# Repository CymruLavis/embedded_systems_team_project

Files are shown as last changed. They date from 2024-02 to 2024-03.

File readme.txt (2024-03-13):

Note to developers: after connecting this repo to your local machine any additional 
class files that need to be used in execution need to be added to the CMakeLists.txt file. That is done by adding 
src/<filename>.cpp to the add_exacutable chain

to run the program make sure you are in the build directory then run the following

>> make
>> ./cocktail_machine

make is the command that will compile the project with our cmake architecture
./cocktail_machine executes/runs the project

SMART DRINKER COCKTAIL MACHINE PROJECT  
![Logo]()

This is our team project for embedded systems at the University of Glasgow with team members:
Ethan Lavis
Daraigh O'Toole Eglington
Joshua Varghese
Roykeane Syangu

The goal of this project is to create an automcatic cocktail dispensor using real time embedded programming on the raspberry pi

![CAD]()

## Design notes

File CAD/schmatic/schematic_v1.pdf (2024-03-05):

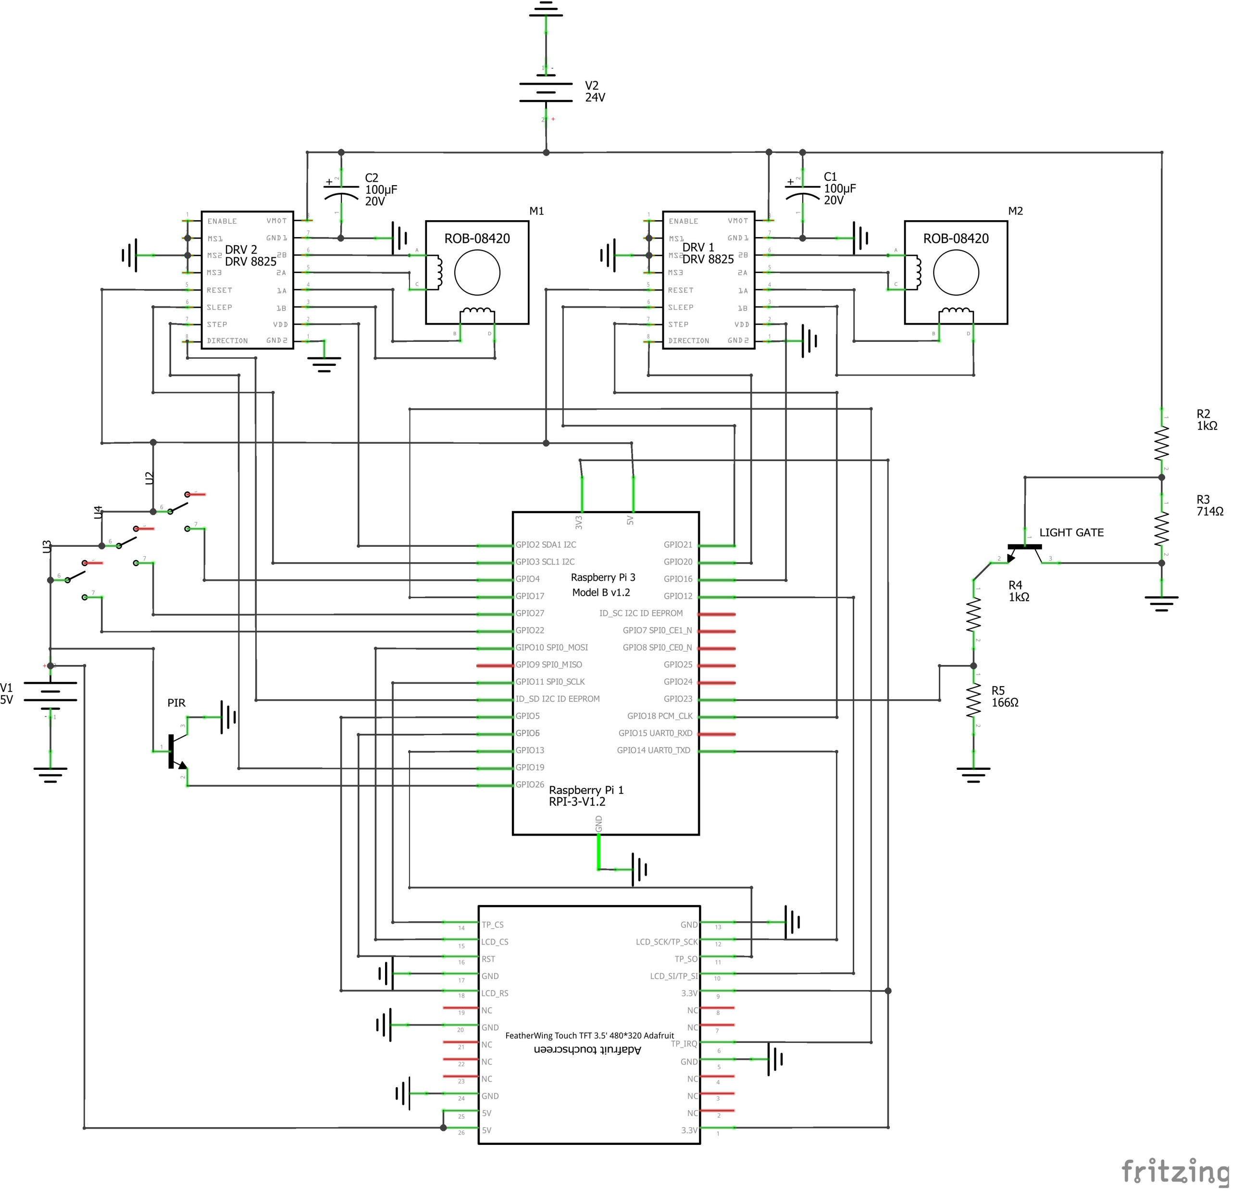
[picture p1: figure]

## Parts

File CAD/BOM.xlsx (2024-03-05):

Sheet: DETAIL_BOM
DESCRIPTION | MANUFACTURER PART NUMBER AND DATA SHEET | QUANTITY | UNIT COST | COST | LINK AND SUPPLIER
VERTICAL ACTUATOR STEPPER DRIVE SET | CABLE PIN OUT TO CONTROLLER IN DATASHEET (https://www.omc-stepperonline.com/3-pcs-e-series-nema-17-bipolar-42ncm-59-49oz-in-1-5a-42x42x38mm-4-wires-w-1m-cable-connector-3-17he15-1504s) | 1 | 14.33 | 14.33 | OMC-STEPPER LINK TO PART CLICK HERE (https://www.omc-stepperonline.com/3-pcs-e-series-nema-17-bipolar-42ncm-59-49oz-in-1-5a-42x42x38mm-4-wires-w-1m-cable-connector-3-17he15-1504s) | https://www.omc-stepperonline.com/e-series-nema-17-bipolar-42ncm-59-49oz-in-1-5a-42x42x38mm-4-wires-w-1m-cable-connector-17he15-1504s
Optic dispensors |  | 6 | 2.75 | 16.5 | ASCOT WHOLESALE LINK TO PART CLICK HERE (https://www.ascotwholesale.co.uk/25ml-black-solo-measure?gad_source=1) | https://www.ascotwholesale.co.uk/25ml-black-solo-measure?gad_source=1
TUBE 8x1.5mm 700mm long. Use the free custom cutting service. |  | 1 | 5.96 | 5.96 | METALS4U LINK TO PART CLICK HERE (https://www.metals4u.co.uk/materials/mild-steel/mild-steel-tube/tube/9135-p) | https://www.metals4u.co.uk/materials/mild-steel/mild-steel-tube/tube/9135-p
Square Box Section 12.7x12.7x1.2 700mm Long Use the free custom cutting service |  | 4 | 1.64 | 6.56 | METALS4U LINK TO PART CLICK HERE (https://www.metals4u.co.uk/materials/mild-steel/mild-steel-box-section/2371-p) | https://www.metals4u.co.uk/materials/mild-steel/mild-steel-box-section/2371-p
MOTION DETECTOR PIR | PIR sensor - works like a switch!! (https://www.mpja.com/download/31227sc.pdf) | 1 | 3 | 3 | PIHIT LINK TO PART CLICK HERE (https://thepihut.com/products/pir-motion-sensor-module) | https://thepihut.com/products/pir-motion-sensor-module | https://shop.pimoroni.com/products/pir-motion-sensor-1?variant=39364784881747
 |  |  | TOTAL: | 46.35
STEPPER MOTOR DRIVER OPTION 1 STEP/DIR | DRV8825 DRIVER DATASHEET (https://www.ti.com/lit/ds/symlink/drv8825.pdf) | 2 | 4.5 | 9 | https://www.amazon.co.uk/DRV8825-Stepper-Suitable-8-2V-45V-Printer/dp/B0CCRXGKLV?hvadid=676281988980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 |  | https://www.pololu.com/product/2133 | https://www.ti.com/lit/ds/symlink/drv8825.pdf | https://how2electronics.com/control-stepper-motor-with-drv8825-raspberry-pi-pico/
RADIAL BEARINGS |  | 4 | 1.25 | 5 | https://www.amazon.co.uk/sourcingmap-Groove-Bearing-Double-Bearings/dp/B07FDYTJS5
THRUST BEARING |  | 2 | 3 | 6 | https://www.amazon.co.uk/sourcingmap-Single-Direction-Thrust-Bearings/dp/B07G8QDQVM
3.5" Touch Screen (mixed reviews, fast shipping, uses 13/20 rows of our pins) | SCREEN DATASHEET/MANUAL (https://www.osoyoo.com/manual/2022013800.pdf) | 1 | 18.99 | 18.99 | https://www.amazon.co.uk/OSOYOO-Monitor-Raspberry-480x320-Interface/dp/B085TC5YMR?rnid=428432031
VELCRO STRAP |  | 1 | 3.2 | 3.2 | https://www.amazon.co.uk/VELCRO%C2%AE-Brand-ONE-WRAP%C2%AE-double-Strapping/dp/B0777LN5VP
 |  |  | TOTAL: | 42.19
MICRO SWITCH | USE A SPDT switch in circuit diagram set to n.o | 1 | FREE | 0
Omron Through Beam Photoelectric Sensor | EE-SX4009-P1 (https://omronfs.omron.com/en_US/ecb/products/pdf/en-ee_sx3009_p1_4009_p1.pdf) | 1 | DARA | 0 | https://uk.rs-online.com/web/p/photoelectric-sensors/8074251
FASTENERS |  |  | DARA | 0
3D PRINTS |  |  | DARA | 0
INSERTS BRASS M3&M4 |  |  | DARA | 0
Total Cost
 | SPDT

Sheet: FASTENERS
M | PART | LENGTH | DEPTH | HEAD WDITH
M4 | NUT | 6.87 | 3 | 6.9 | PART NUMBER | SIZE | TYPE | LENGTH | QTY. | STOCK?
M3 | NUT | 5.4 | 2.23 | 5.45 | DIN 912 M2 x 20 --- 20N | M2 | SKT | 20 | 4 | CHECK
M3 | CSK | 12 |  | 5.5 | Hexagon Nut ISO 4032 - M2 - D - N | M2 | NUT | 5.5 | 8 | YES
M3 | CSK | 20 |  | 5.3 | Hexagon Nut ISO 4032 - M3 - D - N | M3 | NUT | 5.5 | 100
M3 | POSY | 6 |  | 5.9 | DIN 7991 - M3 x 12 --- 8.8N | M3 | CSK | 12 | 21
M3 | POSY | 12 |  | 6 | DIN 912 M3 x 10 --- 10N | M3 | SKT | 10 | 6 | USE M3X12
M4 | CSK | 10 |  | 7.7 | DIN 7991 - M3 x 16 | M3 | CSK | 16 | 50 | ORDER | https://www.amazon.co.uk/ORANXIN-Hex-Bolts-Screws-Countersunk/dp/B08BHL1BBZ?th=1 | https://www.accu.co.uk/order
M4 | CSK | 25 |  | 8.3 | DIN 912 M3 x 12 --- 12N | M3 | SKT | 12 | 32 | HAVE
M4 | POSY | 12 |  | 7.75 | DIN 912 M2 x 6 --- 6N | M2 | SKT | 6 | 4 | CHECK
 |  |  |  |  | DIN 912 M3 x 30 --- 30N | M3 | SKT | 30 | 24 | ORDER |  | https://www.accu.co.uk/metric-cap-head-screws/2805-SSC-M3-30-A2
 |  |  |  |  | Washer DIN 125 - A 3.2 | M3 | WASHER | 1.2 | 24 | HAVE

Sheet: Sheet3
M | PART | LENGTH | DEPTH | HEAD WDITH
M3 | NUT | 5.4 | 2.23 | 5.45
M3 | CSK | 12 |  | 5.5
M3 | POSY | 6 |  | 5.9
M3 | CSK | 20 |  | 5.3
M3 | POSY | 12 |  | 6
M4 | POSY | 12 |  | 7.75
M4 | CSK | 10 |  | 7.7
M4 | NUT | 6.87 | 3 | 6.9
M4 | CSK | 25 |  | 8.3
 |  |  |  |  | M3 | CSK | 12 | 5.5
 |  |  |  |  | M3 | CSK | 20 | 5.3
 |  |  |  |  | M3 | POSY | 6 | 5.9
 |  |  |  |  | M3 | POSY | 12 | 6
 |  |  |  |  | M4 | CSK | 10 | 7.7
 |  |  |  |  | M4 | CSK | 25 | 8.3
 |  |  |  |  | M4 | POSY | 12 | 7.75

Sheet: FASTENER BOM
PART NUMBER | SIZE | TYPE | LENGTH | QTY.
DIN 7991 - M3 x 8 --- 8N | M3 | CSK | 8 | 8
DIN 912 M3 x 10 --- 10N | M3 | SKT | 10 | 8
DIN 912 M3 x 12 --- 12N | M3 | SKT | 12 | 4
DIN 7991 - M3 x 12 --- 8.8N | M3 | CSK | 12 | 8
DIN 7991 - M3 x 16 --- 12.8N | M3 | CSK | 16 | 6
DIN 7991 - M3 x 16 --- 16N | M3 | CSK | 16 | 8
DIN 912 M3 x 16 --- 16N | M3 | SKT | 16 | 4
DIN 7991 - M4 x 16 --- 16N | M3 | CSK | 16 | 18
DIN 912 M3 x 25 --- 18N | M3 | SKT | 25 | 24
DIN 7991 - M3 x 30 --- 12N | M3 | CSK | 30 | 4

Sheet: SPIN VS PUMPED
 | Weighting: | SPINNING | SUM: | PUMPED | SUM: | BOM PUMPED SOLTUON | QUANTITY | UNIT COST | TOTAL COST | LINK
SPEED | 1 | 2 | 2 | 2 | 2 | 12V MOTORS | 6 | 4 | 24
COST | 1 | 3 | 3 | 1 | 1 | BEARINGS | 18 | 0.25 | 4.5
MECHANICAL COMPLEXITY | 1 | 1 | 1 | 3 | 3 | PLASTIC | 0 | 0 | 0
SOFTWARE COMPLEXITY | 1 | 2 | 2 | 2 | 2 | FLEXIBLE TUBING | 5 | 1.52 | 7.6
SCALABILITY | 1 | 1 | 1 | 3 | 3 | 120W PSU | 1 | 20 | 20
COOLNESS | 1 | 3 | 3 | 1 | 1 | Motor control relay board | 11 | 1 | 11
NOISE | 1 | 3 | 3 | 1 | 1 | Webcam | 1 | 0 | 0 | have
TOTAL: |  | 15 |  | 13 |  | Cables | 0 | 0 | 0 | FROM SCHOOL
 |  |  |  |  |  | Fasteners | 0 | 0 | 0 | FROM SCHOOL
 |  |  |  |  |  | Plywood | 0.5 | 10 | 5
 |  |  |  |  |  | TOTAL: |  |  | 72.1
 |  |  |  |  |  | SPINNING SOLUTION | QUANTITY | UNIT COST | TOTAL COST
 |  |  |  |  |  | STEPPER MOTOR | 2 | 10 | 20
 |  |  |  |  |  | STEPPER MOTOR DRIVER | 2 | 5 | 10
 |  |  |  |  |  | THRUST BEARING | 1 | 3 | 3
 |  |  |  |  |  | RADIAL BEARING | 1 | 0 | 0
 |  |  |  |  |  | MICRO SWITCHES | 6 | 0.2 | 1.2
 |  |  |  |  |  | Velcro | 2 | 2 | 4
 |  |  |  |  |  | Filament | 0 | 0 | 0
 |  |  |  |  |  | Steel Bar | 2.5 | 2.5 | 6.25
 |  |  |  |  |  | Dispensers | 6 | 3 | 18
 |  |  |  |  |  | PSU | 1 | 10 | 10
 |  |  |  |  |  | Fasteners | 0 | 0 | 0
 |  |  |  |  |  | Cables | 0 | 0 | 0
 |  |  |  |  |  | Webcam | 0 | 0 | 0
 |  |  |  |  |  | TOTAL: |  |  | 72.45

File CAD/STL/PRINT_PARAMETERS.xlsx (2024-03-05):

COMPONENT NAME: | QUANTITY | VOLUME: L*W*H (mm) | SUPPORTS: | ORIENTATION SPECIFIC: | LAYER HEIGHT: | EXTRUSION WIDTH: | INFILL/PERIMETER OVERLAP: | INFILL: | # PERIMETERS: | SOLID LAYERS: TOP AND BOTTOM | MATERIAL:
SQUARE TUBE BRACKET | 8 | 50x50x30 | NO | YES | 0.2 | 0.5 | 25% | 15% | 5 | 4 | PLA/PETG/ABS
BRACKET_THROUGH | 4 | 50x50x30
MID_PANEL | 1 | 255x255x5
TOP_PLATE | 1 | 255x255x5

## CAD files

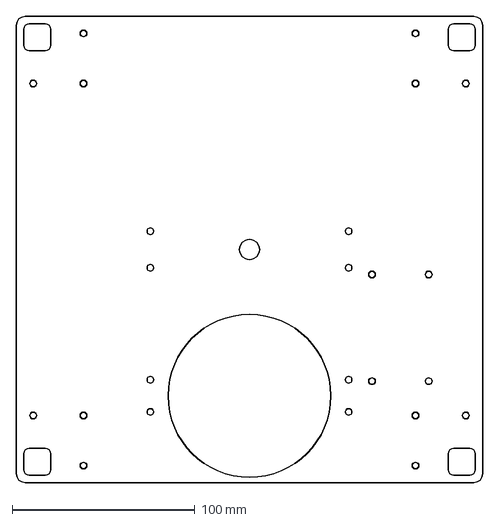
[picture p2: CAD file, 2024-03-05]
CAD/DXF/5MM_MID_PANEL.DXF
255.0 x 255.0 mm

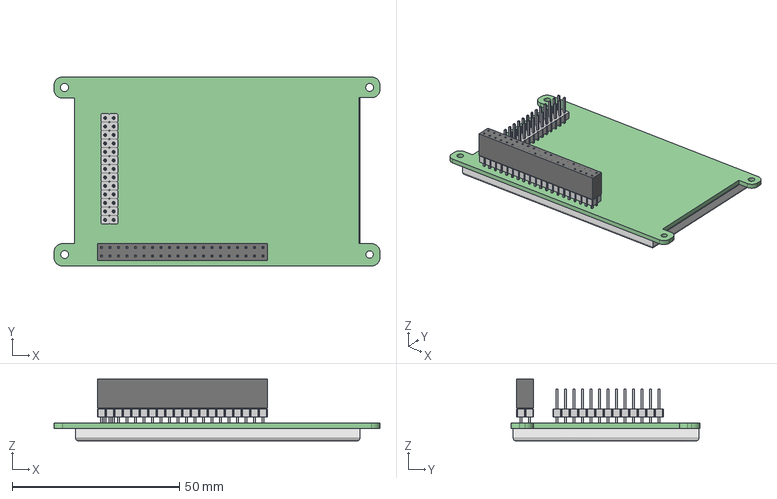
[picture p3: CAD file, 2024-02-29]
CAD/step files/PiTFT PLUS 3.5inch.stp
97.5 x 56.5 x 18.5 mm
PIN_STRIP-2_54 x 33

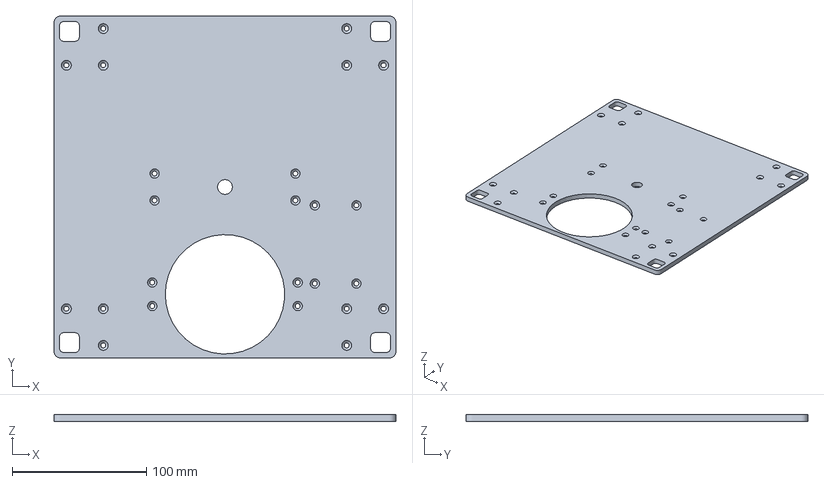
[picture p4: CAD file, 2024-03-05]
CAD/STL/mid_panel.3MF
255.0 x 255.0 x 5.00 mm

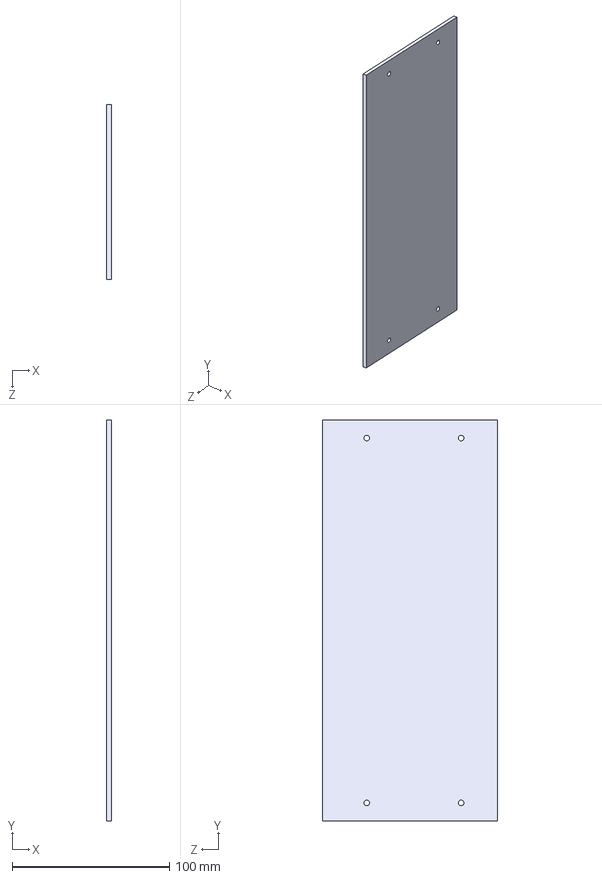
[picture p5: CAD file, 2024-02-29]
CAD/step files/SIDE_PANEL.STEP
3.00 x 255.0 x 111.0 mm

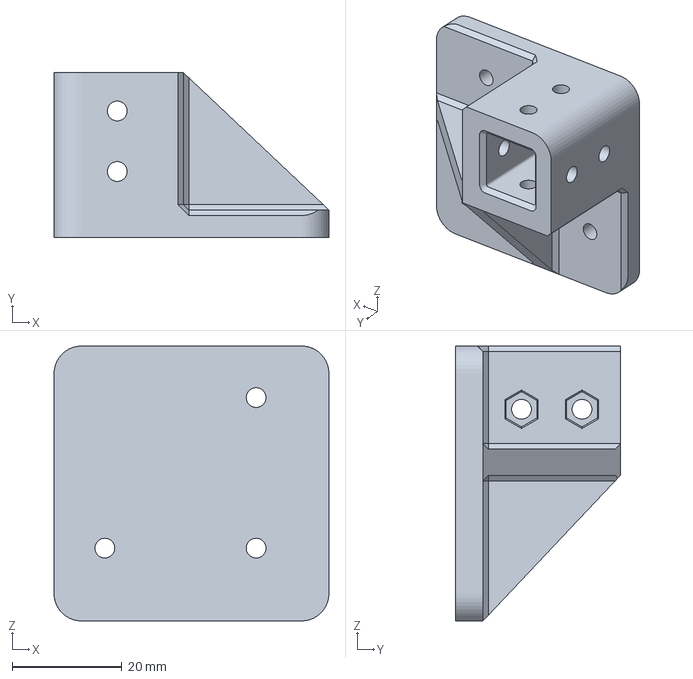
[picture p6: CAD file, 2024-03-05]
CAD/STL/SQUARE TUBE BRACKET.3MF
50.0 x 30.0 x 50.0 mm

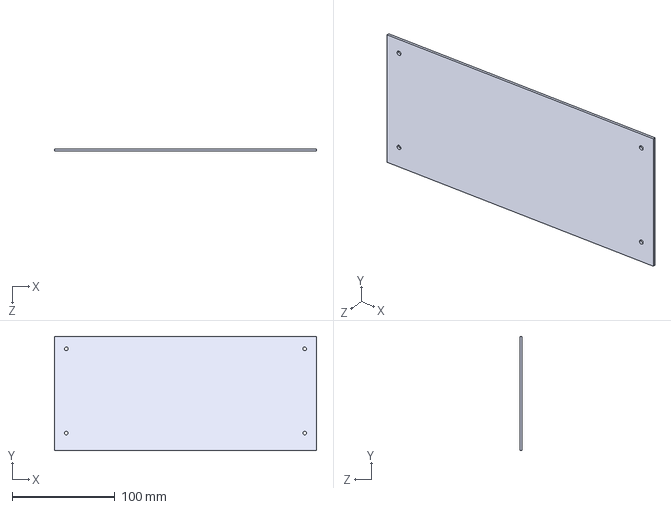
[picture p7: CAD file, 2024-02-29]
CAD/step files/BACK_PANEL.STEP
255.0 x 111.0 x 2.00 mm

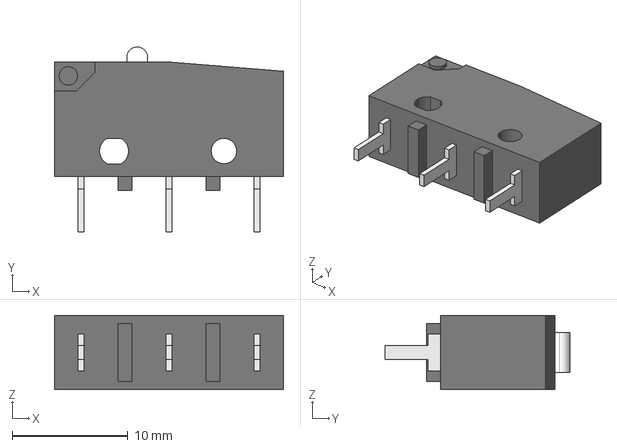
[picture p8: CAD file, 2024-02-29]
CAD/step files/ssg-5p-5.stp
19.8 x 16.0 x 6.40 mm

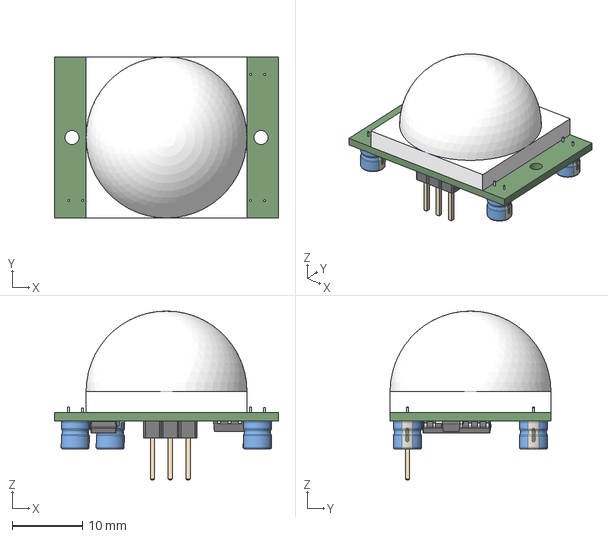
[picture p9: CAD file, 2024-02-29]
CAD/step files/D-SUN-IRdetector1.step
32.0 x 23.0 x 24.1 mm

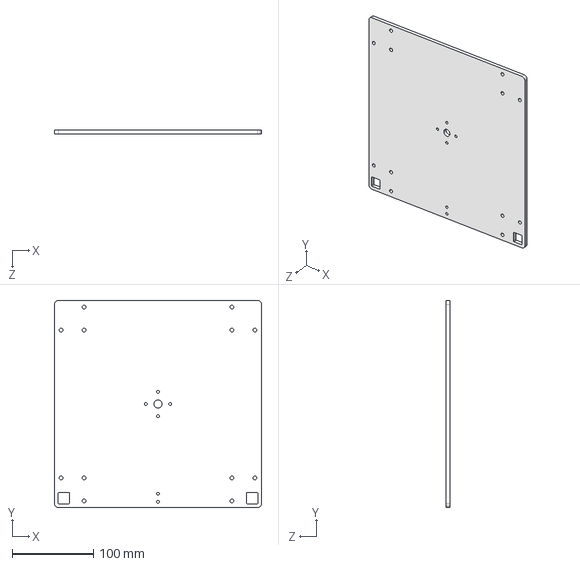
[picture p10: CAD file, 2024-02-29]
CAD/step files/TOP_PLATE.STEP
255.0 x 255.0 x 5.00 mm

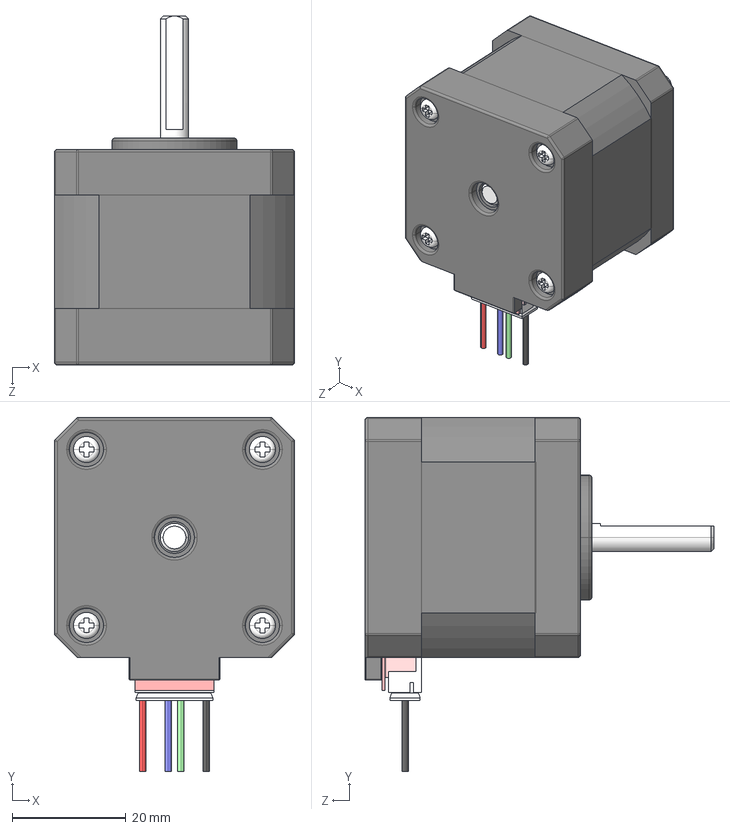
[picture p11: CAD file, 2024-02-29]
CAD/step files/17HE15-1504S.STEP
42.3 x 62.4 x 61.5 mm

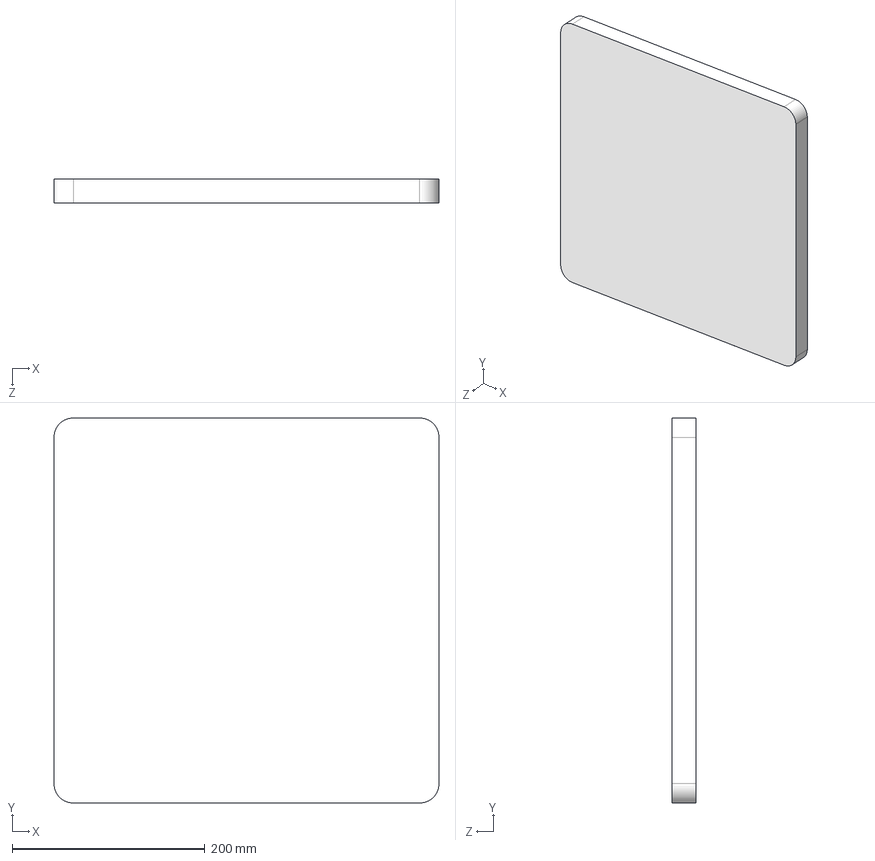
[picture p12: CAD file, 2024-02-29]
CAD/step files/WIDE_BASE.STEP
400.0 x 400.0 x 25.0 mm

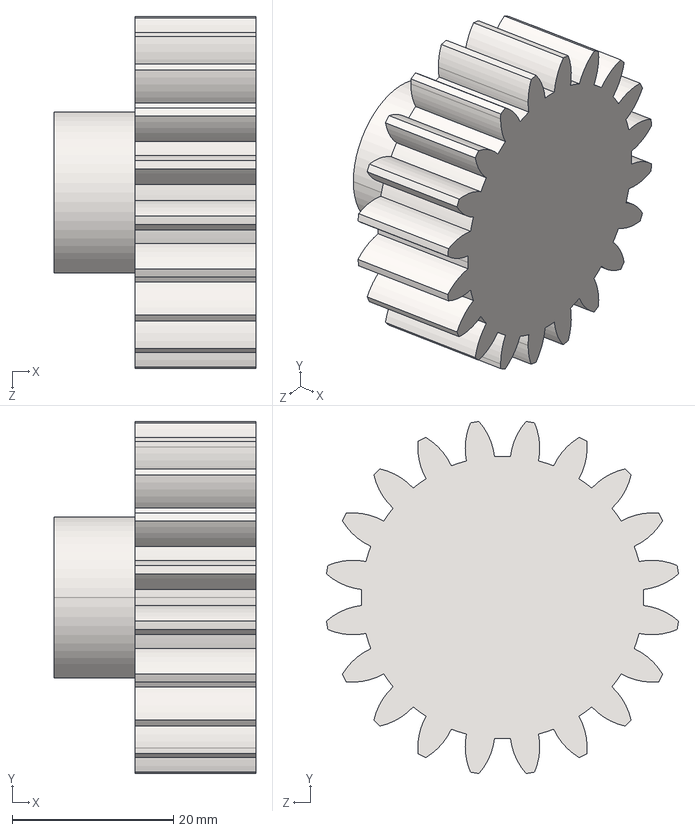
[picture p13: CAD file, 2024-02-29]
CAD/step files/MAN_AXLE_DRIVE_GEAR_2M_20T.STEP
25.0 x 43.6 x 43.6 mm

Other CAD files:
CAD/STL/BRACKET_THROUGH.3MF
CAD/DXF/BACK_PANEL.DXF
CAD/DXF/MID_PANEL.DXF
CAD/DXF/SIDE_PANEL.DXF
CAD/DXF/TOP_PLATE.DXF
CAD/DXF/WIDE_BASE.DXF
CAD/STL/BRACKET_THROUGH.STL
CAD/STL/SQUARE TUBE BRACKET.STL
CAD/STL/TOP_PLATE.3MF
CAD/STL/TOP_PLATE.STL
CAD/STL/mid_panel.STL

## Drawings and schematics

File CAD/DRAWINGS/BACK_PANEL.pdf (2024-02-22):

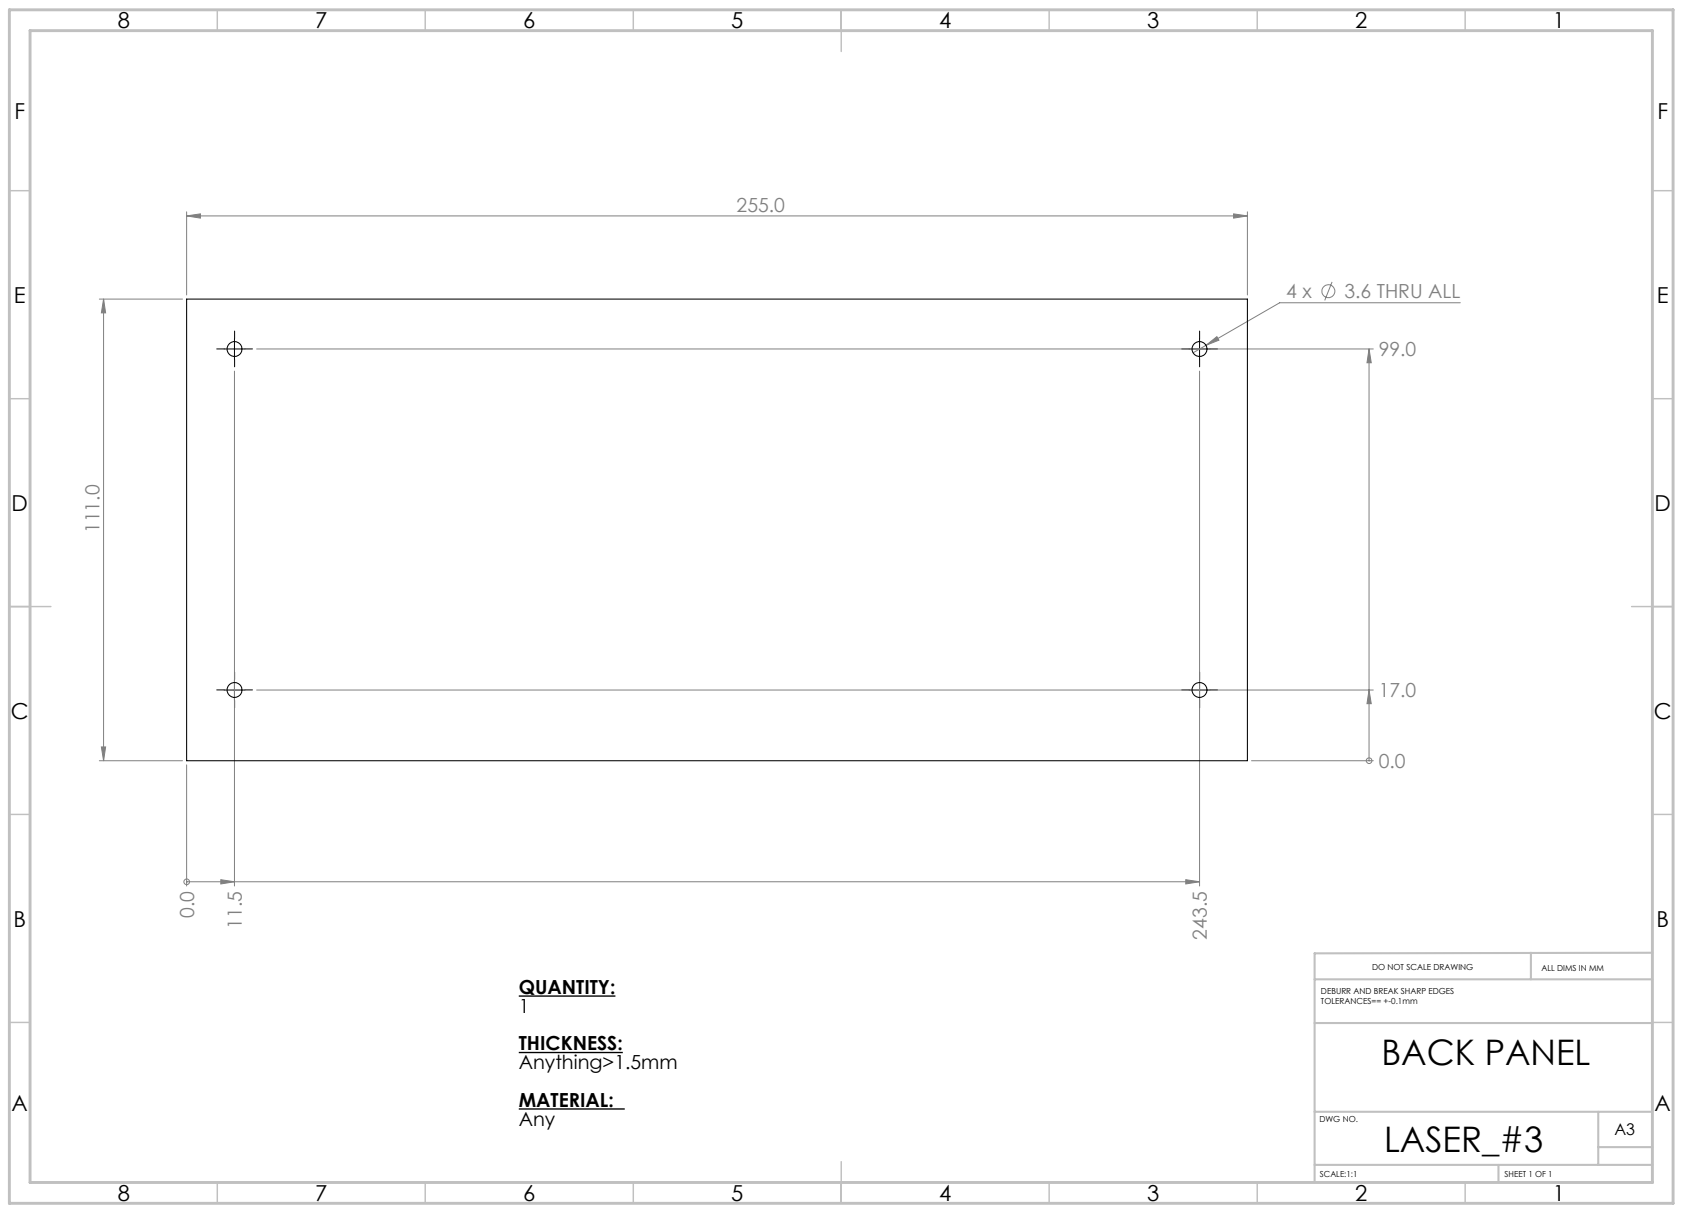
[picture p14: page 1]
3.6 THRU ALL; DO NOT SCALE DRAWING; ALL DIMS IN MM; DWG NO.; SCALE:1:1; SHEET 1 OF 1; BACK PANEL

DEBURR AND BREAK SHARP EDGES
TOLERANCES== +-0.1mm

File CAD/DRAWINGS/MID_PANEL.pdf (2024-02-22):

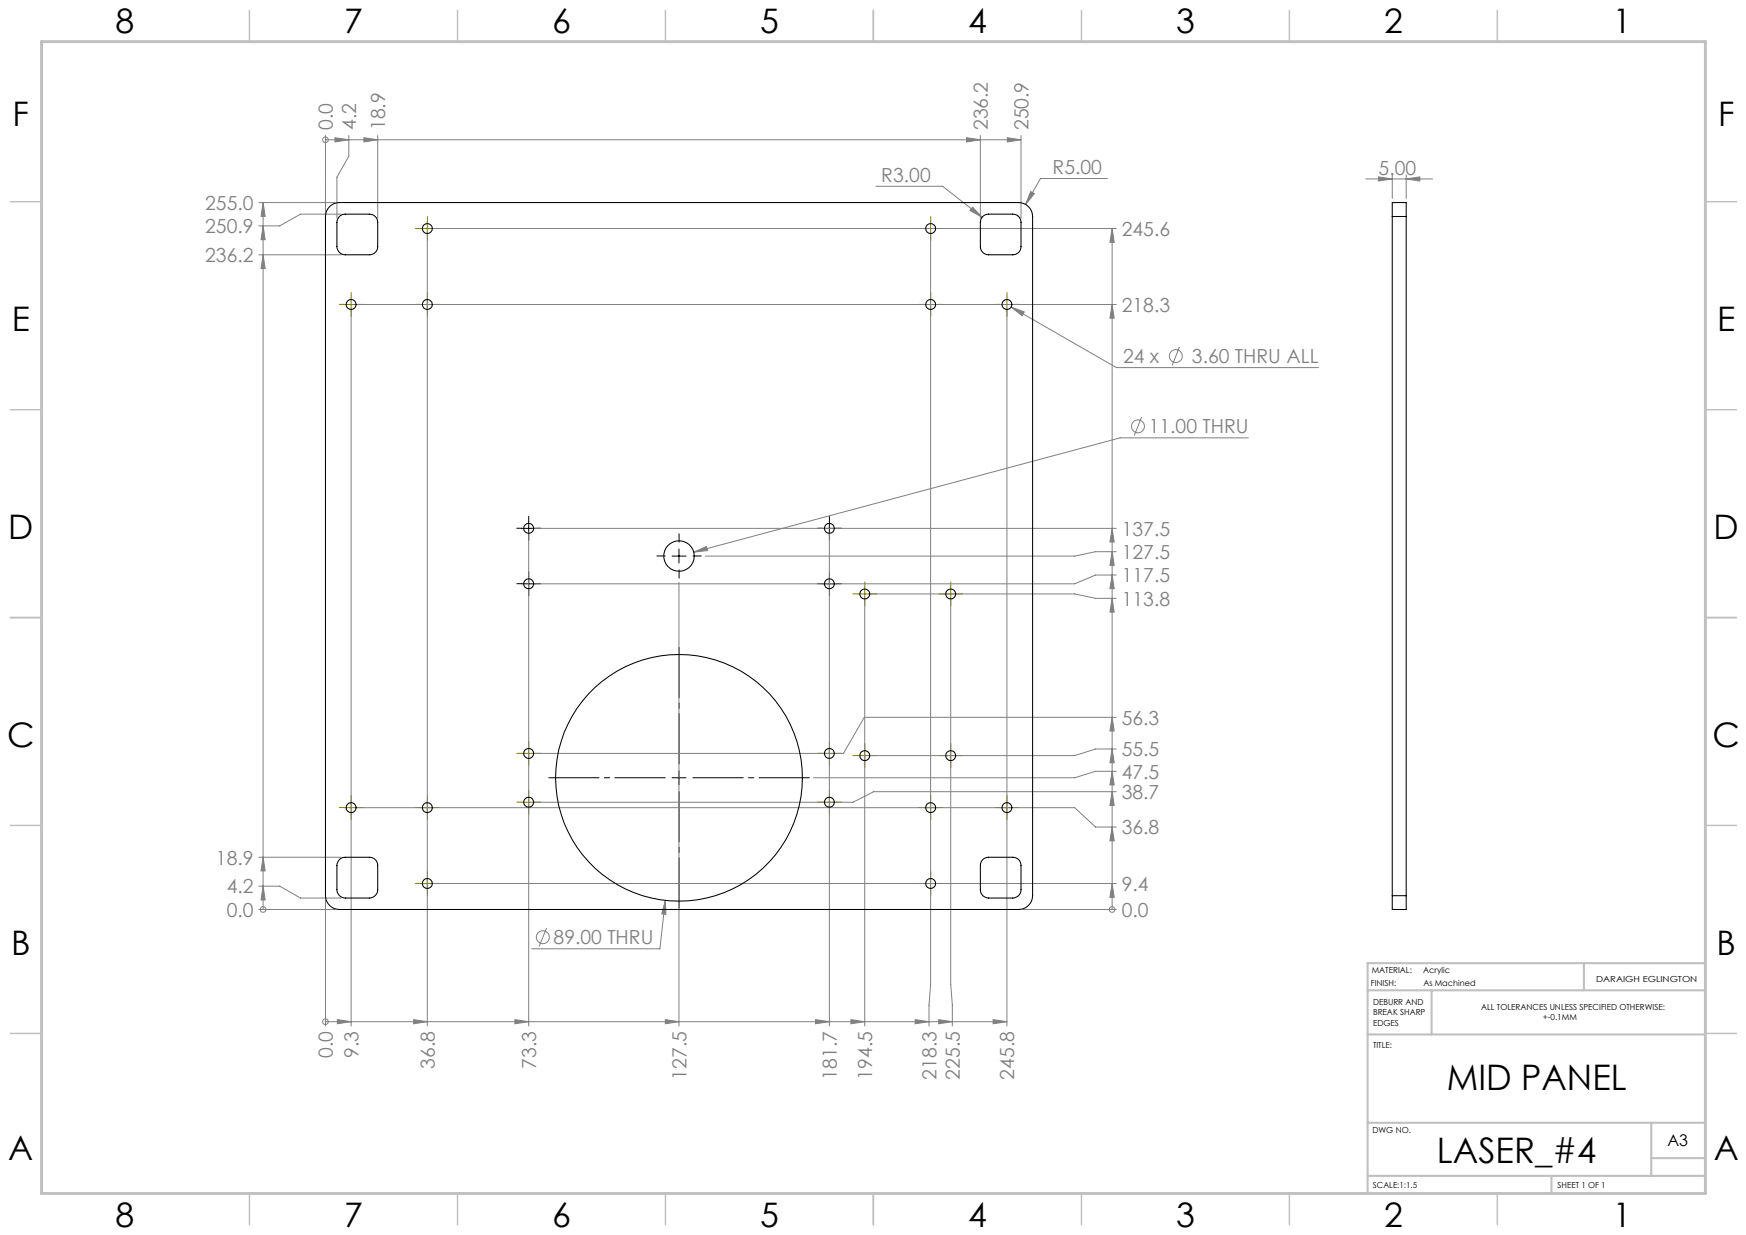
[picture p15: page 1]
3.60 THRU ALL; 89.00 THRU; 11.00 THRU; DWG NO.; SCALE:1:1.5; SHEET 1 OF 1; MID PANEL

MATERIAL: Acrylic FINISH: As Machined | DARAIGH EGLINGTON

DEBURR AND BREAK SHARP EDGES | ALL TOLERANCES UNLESS SPECIFIED OTHERWISE: +-0.1MM

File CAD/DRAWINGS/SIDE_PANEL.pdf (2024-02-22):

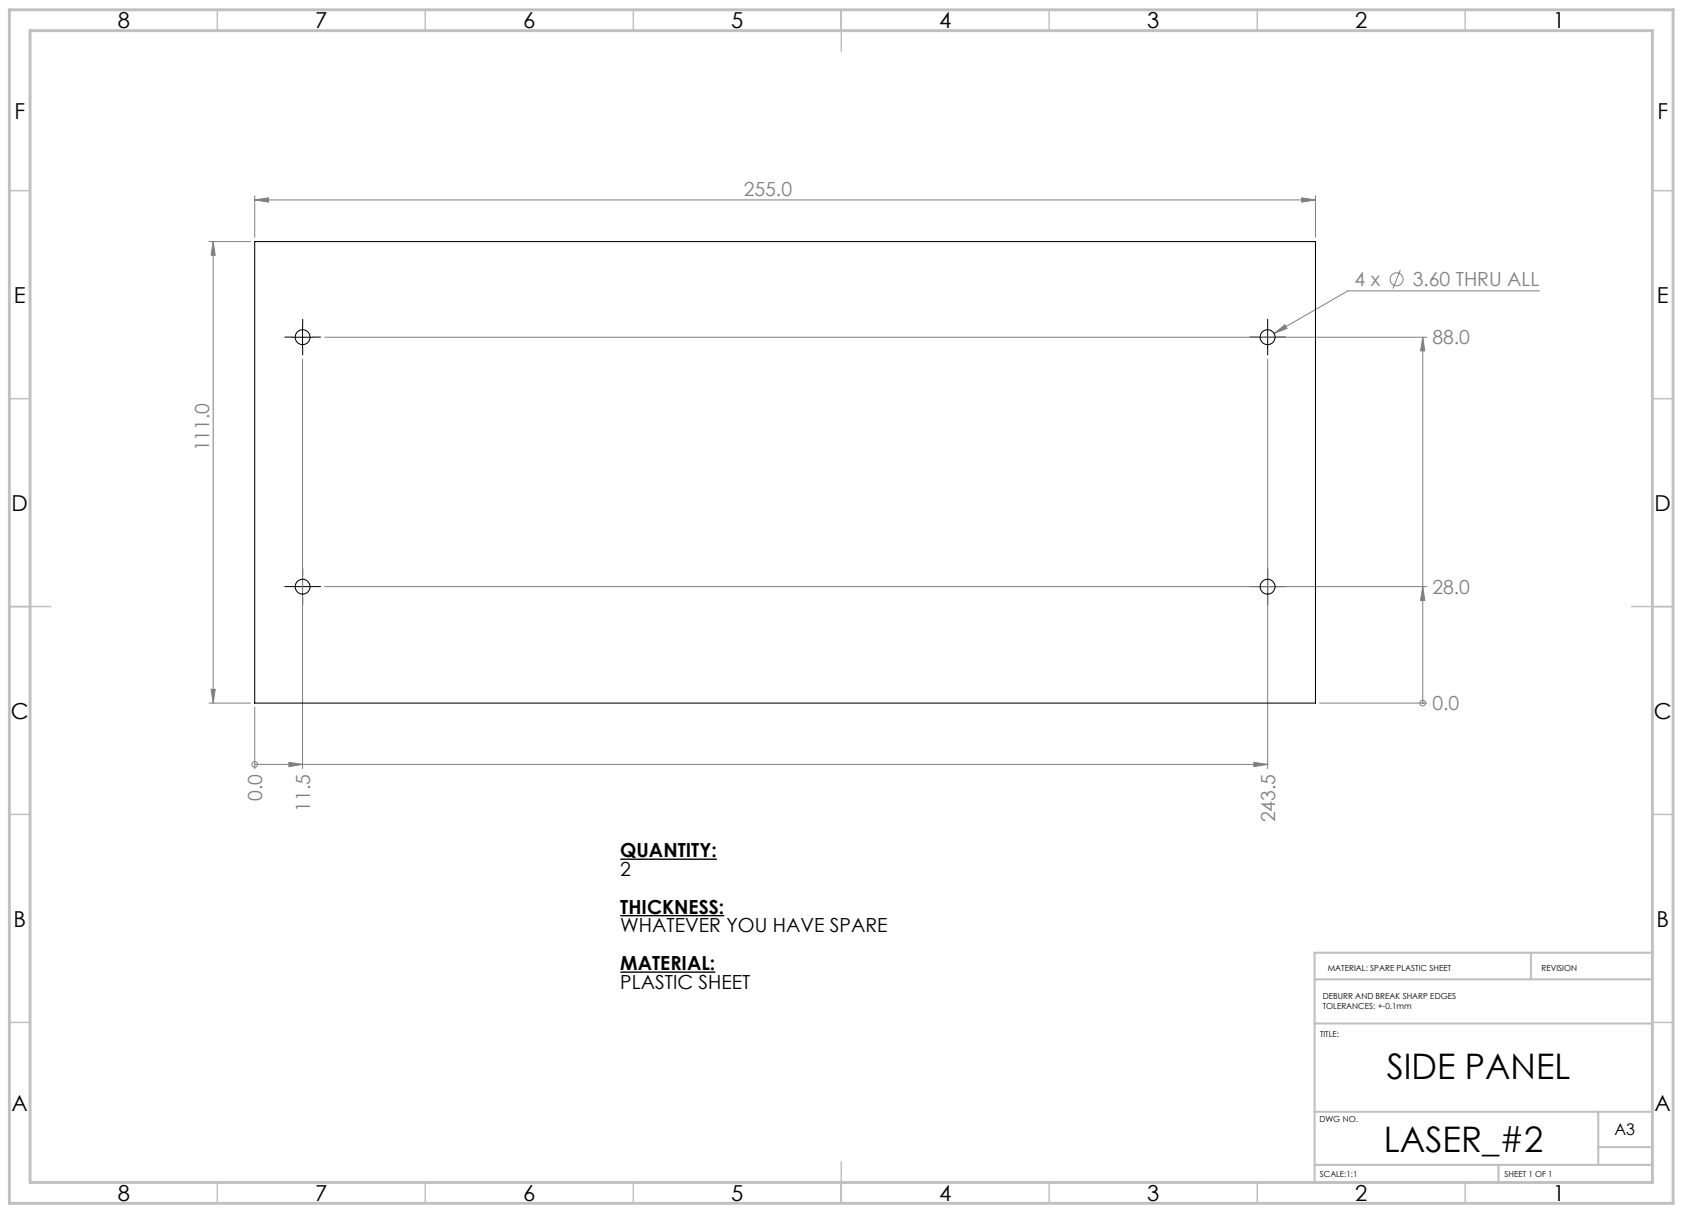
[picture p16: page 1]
3.60 THRU ALL; MATERIAL: SPARE PLASTIC SHEET; REVISION; DWG NO.; SCALE:1:1; SHEET 1 OF 1; SIDE PANEL

QUANTITY:
THICKNESS:
WHATEVER YOU HAVE SPARE
MATERIAL:
PLASTIC SHEET

DEBURR AND BREAK SHARP EDGES
TOLERANCES: +-0.1mm

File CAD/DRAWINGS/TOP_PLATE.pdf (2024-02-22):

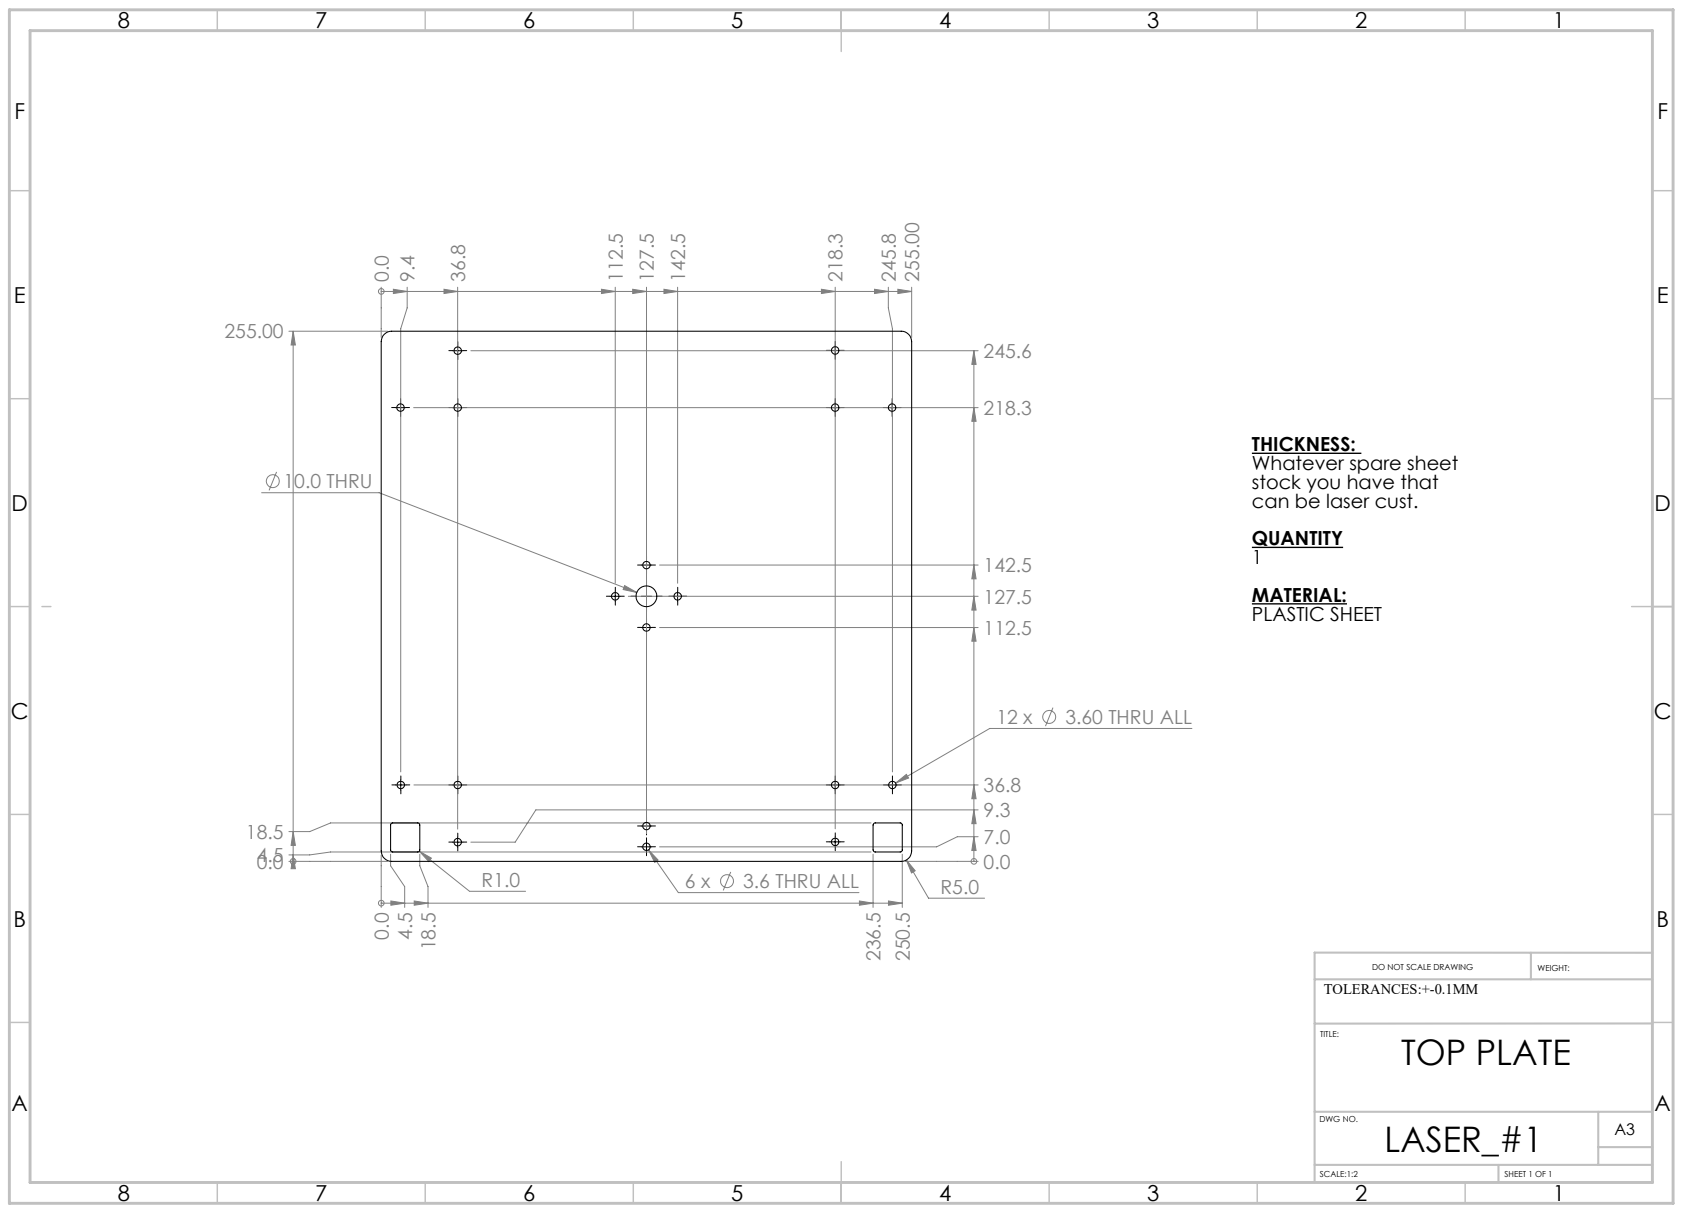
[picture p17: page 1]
3.6 THRU ALL; 3.60 THRU ALL; 10.0 THRU; DWG NO.; SCALE:1:2; SHEET 1 OF 1

THICKNESS:
Whatever spare sheet
stock you have that
can be laser cust.
QUANTITY
MATERIAL:
PLASTIC SHEET

DO NOT SCALE DRAWING
TOLERANCES:+-0.1MM
TOP PLATE
LASER_#1

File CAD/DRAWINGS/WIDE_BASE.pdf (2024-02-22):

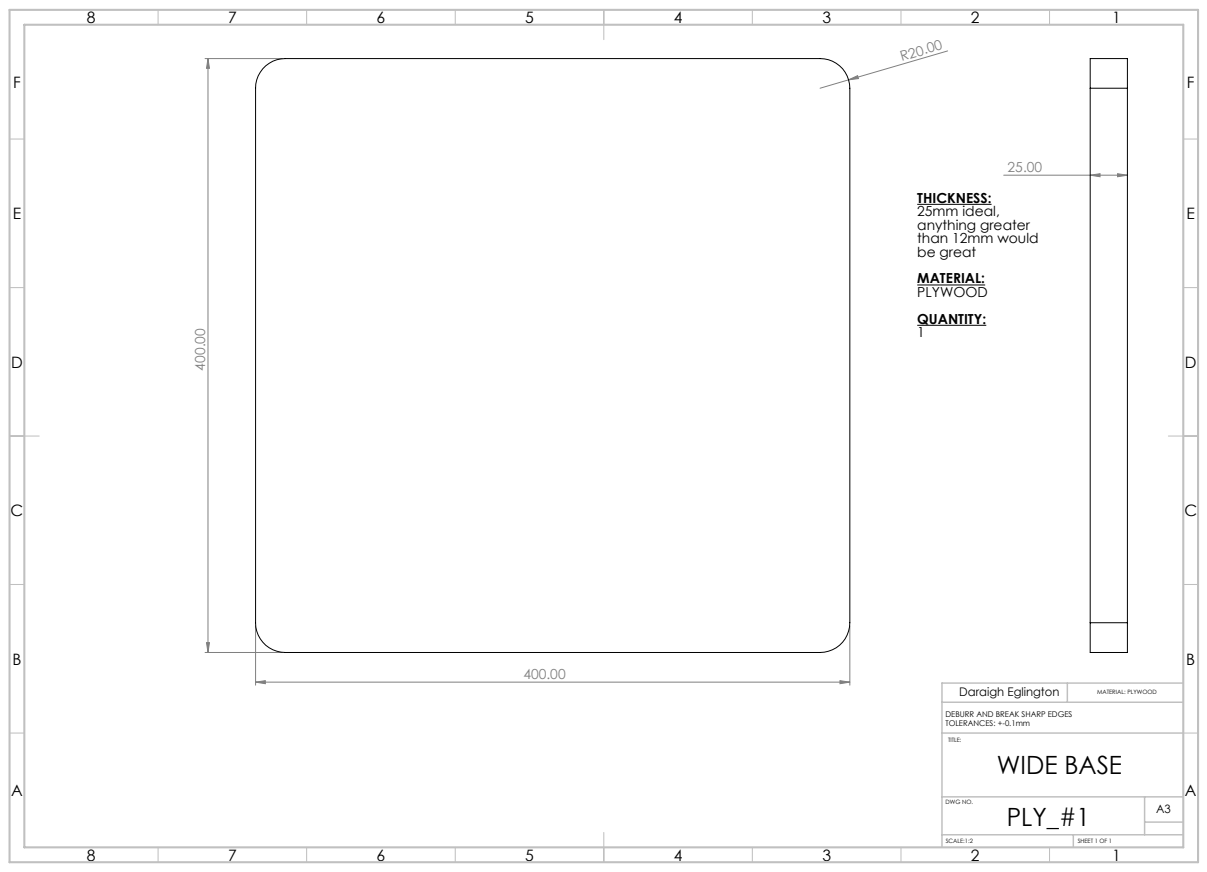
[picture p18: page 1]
25mm ideal, anything greater than 12mm would be great; QUANTITY: 1; Daraigh Eglington; MATERIAL: PLYWOOD; SCALE:1:2; SHEET 1 OF 1

DEBURR AND BREAK SHARP EDGES
TOLERANCES: +-0.1mm

TITLE: WIDE BASE

DWG NO. PLY_#1 | A3

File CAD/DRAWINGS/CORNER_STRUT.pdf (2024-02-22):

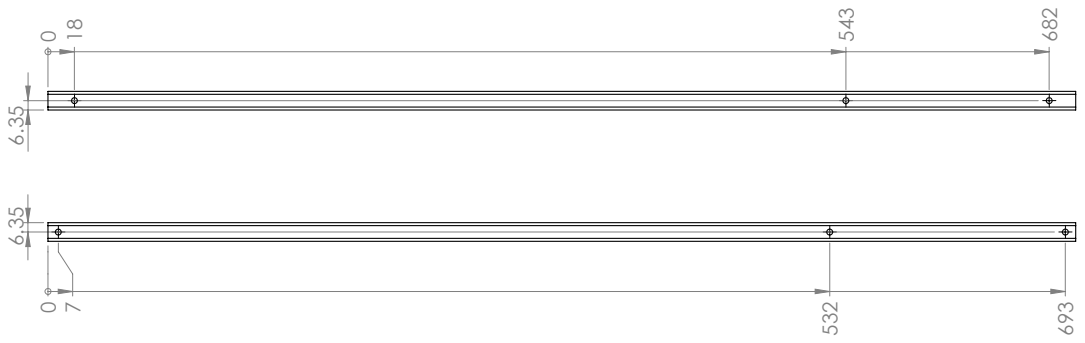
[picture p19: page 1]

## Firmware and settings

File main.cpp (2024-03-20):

#include <iostream>
#include "Include/Data.h"
#include "Include/SystemConfig.h"
#include "Include/Motor.h"

using namespace std;

void printDF(vector<vector<string>> df){
	for (const auto& row : df) {
		for (const auto& str : row) {	
			cout << str << "\t";
		}
		cout << endl;
	}
}
void printList(vector<string> list){
	for (const auto& str : list) {
		cout << str << endl;
	}
}
void printListOfInts(vector<int> list){
	for (const auto& str : list) {
		cout << str << endl;
	}
}
void printColum(vector<vector<string>> list){
	for (const auto& str : list) {
		cout << str[1] << endl;
	}
}
void setIngredientPositions(Data *myData, SystemConfig *sys, vector<string> const *ingredients){
	int index = 0;
	for(auto& ing: *ingredients){
		int temp_ingredient_idx = myData->ingredientToIndex(ing);
		sys->updatePosition(index, temp_ingredient_idx);
		cout << index << "\t" << temp_ingredient_idx << "\t" << ing << endl;
		index ++;
	}

}
void printSys(SystemConfig sys){
	for(auto& ing: sys.positions){
		cout << ing.getIngredient() << "\t" << ing.getPosition() << endl;
		// int a = 2, b = 4;
		// ing.setIngredient(a);
		// ing.setPosition(b);
		// cout << ing.ingredient << "\t" << ing.position << endl;

	}
}
int main(){

	Data* myData = new Data();
	SystemConfig* sys = new SystemConfig();
	Motor* myMotor = new Motor(1,2,3,4, 1.8);

	vector<vector<string>> df = myData->df_menu;
	vector<vector<string>> ing_df = myData->ingredient_indexes.df;
	vector<string> ing = myData->ingredient_indexes.ingredients;
	vector<string> idx = myData->ingredient_indexes.indexes;

	vector<string> system_ingredients = {"Vodka","Gin", "Cointreau", "Cranberry Juice", "Mezcal","Lime Juice"};
	setIngredientPositions(myData, sys, &system_ingredients);

	printSys(*sys);

	string desired_drink = "Cosmopolitan";
	vector<int> drink_queue = myData->getRecipe(desired_drink, *sys);

	vector<int> step_queue = myMotor->getStepQueue(drink_queue);

	printListOfInts(drink_queue);

	// get currecnt position
	// calculate degrees between current and desired
	//spin to position
	return 0;

}



// int main(){
// MOTOR TEST
// }


// #include<iostream>
// #include "SWITCH_CONTROL_H.h"
// #include <iostream>
// #include  <pigpio.h>
// #include  <thread>

// void switchMonitor (int switchIndex, SwitchControl& switchControl){
//      while (true) {
//         if (switchControl.isSwitchOn(switchIndex)){
//             std::cout<<"Switch "<<switchIndex+1<<"IS ON/n";
//         }else {
//             std::cout<<"Switch "<<switchIndex+1<<"IS OFF/n";
//         }
//      }
//  }
    
    


// int main() {
    
//      std::vector<int>SwitchPins = {7,13,15};
//      SwitchControl switchControl (SwitchPins);

//      if(!switchControl.intialize()){
//         std::cout<<"initialization failed.\n";
//         return 1;
//      }
//      std::vector<std::thread> threads;
//      for (int i= 0; i < SwitchPins.size();i++){
//          threads.emplace_back(switchMonitor , i, std::ref(switchControl));
//      }
//      //waiting for the threads to finish of which it never does
//      for(std::thread& t:threads) {
//          t.join();
//      }
     
     

//     return 0;

// }

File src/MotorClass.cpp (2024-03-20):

#include "../Include/Motor.h"
#include <pigpio.h>

#include <iostream>
#include <unistd.h>
#include <vector>
#include <math>

Motor::Motor(int dir, int step, int sleep, int fault, double step_size){
    Motor::setDirPin(dir);
    Motor::setStepPin(step);
    Motor::setSleepPin(sleep);
    Motor::setFaultPin(fault);
	Motor::initializePins(dir, step, sleep, fault);

	Motor::step_angle = step_size;
	Motor::setMotorCharacteristics(Motor::step_angle);


}
void Motor::setMotorCharacteristics(double step_angle){
	this->step_per_rev = 360/step_angle;
}
void Motor::setDirPin(int pin){
    this->direction_pin = pin;
}
int Motor::getDirPin(){
    return this->direction_pin;
}
void Motor::setStepPin(int pin){
    this->step_pin = pin;
}
int Motor::getStepPin(){
    return this->step_pin;
}
void Motor::setSleepPin(int pin){
    this->sleep_pin = pin;
}
int Motor::getSleepPin(){
    return this->sleep_pin;
}
void Motor::setFaultPin(int pin){
    this->fault_pin = pin;
}
int Motor::getFaultPin(){
    return this->fault_pin;
}

void Motor::setDirState(int val){
    this->dir_state = val;
}
int Motor::getDirState(){
    return this->dir_state;
}
void Motor::setStepState(int val){
    this->step_state = val;
}
int Motor::getStepState(){
    return this->step_state;
}
void Motor::setSleepState(int val){
    this->sleep_state = val;
}
int Motor::getSleepState(){
    return this->sleep_state;
}
void Motor::setFaultState(int val){
    this->fault_state=val;
}
int Motor::getFaultState(){
    return this->fault_state;
}
void Motor::setStepPerRev(int val){
    this->step_per_rev = val;
}
int Motor::getStepPerRev(){
    return this->step_per_rev;
}
void Motor::setStepAngle(double val){
    this->step_angle = val;
}
double Motor::getStepAngle(){
    return this->step_angle;
}
void Motor::initializePins(int dir, int step, int sleep, int fault){
    gpioSetMode(dir, PI_OUTPUT);
    gpioSetMode(step, PI_OUTPUT);
    gpioSetMode(sleep, PI_OUTPUT);
    gpioSetMode(fault, PI_OUTPUT);

}
void Motor::step(){
    gpioWrite(this->getStepPin(), 1);
    usleep(1000);
    gpioWrite(this->getStepPin(), 0);
    usleep(1000);
}

int Motor::decideDirection(int currentPos, int desiredPos){
	return 0;
}

int Motor::getDistanceBetweenPositions(int currentPos, int desiredPos){

    int distanceBetweenPostion = std::abs(currentPos-desiredPos);
    
    return distanceBetweenPostion;

}
double Motor::getDegreesToSpin(int distanceBetweenPositions){
   double degreesToSpin = distanceBetweenPositions * 60; 
    return degreesToSpin;

}
int Motor::getStepsToRotoate(double degreesToSpin){
    double step_angle = this->getStepAngle();
    int steps = degreesToSpin/step_angle;

    return steps;

}

vector<int> Motor::getStepQueue(vector<int> positionQueue){
    vector<int> step_queue;
    int currentPos = 0;
    for(int i = 0; i < positionQueue.size(); i++){
        int dist = Motor::getDistanceBetweenPositions(currentPos, positionQueue[i]);
        double deg_to_rototae = Motor::getDegreesToSpin(dist);
        int steps = Motor::getStepsToRotoate(deg_to_rototae);
        step_queue.push_back(steps);
        currentPos = positionQueue[i];
    }

    return step_queue;
}

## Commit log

2024-02-15 created the front end UI
    [target-cocktail_machine_front_end-Debug-3d75df0b3f25c13284b5.json, target-cocktail_machine_front_end_autogen-Debug-3c82e1136c8cde3e3700.json, target-cocktail_m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]
2024-02-16 created the screens with their appropriate widgets
    [Cocktail table.xlsx, target-cocktail_machine_front_end-Debug-12fb310cc8ec32a457a0.json, target-cocktail_machine_front_end-Debug-3d6393e27df066ed16a9.json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]
2024-02-21 built the structure for the backend that will connect to the mySQL database
    [Cocktail table.csv, Cocktail table.xlsx]
2024-02-26 so longer using mySQL, changed to loading data from a csv directly into a 2d array and accessing the data in the same class structure
    [Cocktail table.csv, cocktail_table.csv]
2024-02-27 dxf laser cut files
    [BACK_PANEL.DXF, MID_PANEL.DXF, SIDE_PANEL.DXF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]
2024-02-27 built out the functions of the data class
    [cocktail_table.csv]
2024-02-28 progressed through the back end development, added encoding to menu and created sensor and actuator classes
    [Cocktail table.xlsx, cocktail_table.csv, cocktail_table.xlsm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]
2024-02-29 some step files related to cad.
    [17HE15-1504S.STEP, BACK_PANEL.STEP, D-SUN-IRdetector1.step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]
2024-03-01 3dp stls for hardware
    [BRACKET_THROUGH.3MF, BRACKET_THROUGH.STL, PRINT_PARAMETERS.xlsx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]
2024-03-04 final cad and revised DXF's
    [5MM_MID_PANEL.DXF, BACK_PANEL.DXF, SIDE_PANEL.DXF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]
2024-03-04 schematic v1 and BOM v1
    [BOM.xlsx]
2024-03-05 memory storage classes have their sturcture complete. Still small error to fix in Data class
    [cocktail_table.csv, cocktail_table.xlsm, index_table.csv]
2024-03-05 made the rest of the sensor and actuator class skeletons. Created the GUI.cpp file for the QT GUI
2024-03-11 added to motor class. It is ready to test spinning the motor. Almost ready to test thread and interrupt with a limit swtich
2024-03-13 cleaned up and removed redundant directories
    [target-cocktail_machine_front_end-Debug-12fb310cc8ec32a457a0.json, target-cocktail_machine_front_end-Debug-3d6393e27df066ed16a9.json, target-cocktail_machine_f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]
2024-03-20 make motor logic structure
2024-03-20 light gate class modified to initialize the pin and get the state
